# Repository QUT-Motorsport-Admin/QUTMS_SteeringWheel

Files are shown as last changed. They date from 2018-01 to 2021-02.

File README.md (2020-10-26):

QUTMS_Banner

# QUT Motorsport - Steering Wheel

### What?
A 'dumb' output terminal that acts as a digital dashboard for the car.
### Why?
To display information from the Chassis Controller (originating from various car sensors and systems) to the driver.
### How?
The steering wheel receives information over CANBUS from the Chassis Controller and displays the information relevant to the currently selected mode on a digital display. There will be two cylindrical switches that can be rotated to set the program to different modes allowing for the driver to view different sets of information on the display at will.
### Where?
A digital display in the steering wheel of the car that receives and displays information from other car systems to the driver.
### Who?
*Insert anyone who has worked on the software here.*

## Specific README's
These will cover any specific features, outlines or documentation that a programmer/designer should know about. Any specifics, or this outside the overview/outline please update an entry in the wiki

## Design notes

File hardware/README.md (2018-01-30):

# Steering Wheel Hardware

No hardware yet

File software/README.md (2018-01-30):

# Steering Wheel Software

The steering wheel could be considered a dumb terminal that shows the status of the car. It will be the only way to view the systems in the car aside from the C# program.

It will allow you to shift though the multiple modes that the Chassis Controller ([QUTMS_ChassisController](https://github.com/Technosasquach/QUTMS_ChassisController "QUTMS_ChassisController")) is capable off. It would then update the display and dash to what is best suited for the mode. Additonaly it could be programmed with different interfaces that show various elements of the car to the driver while racing. 

If you are working on this code, then its recommended that you talk to someone that would be driving, so you can tailor the software to their needs.

Below is a rough outline of its operations procedures.

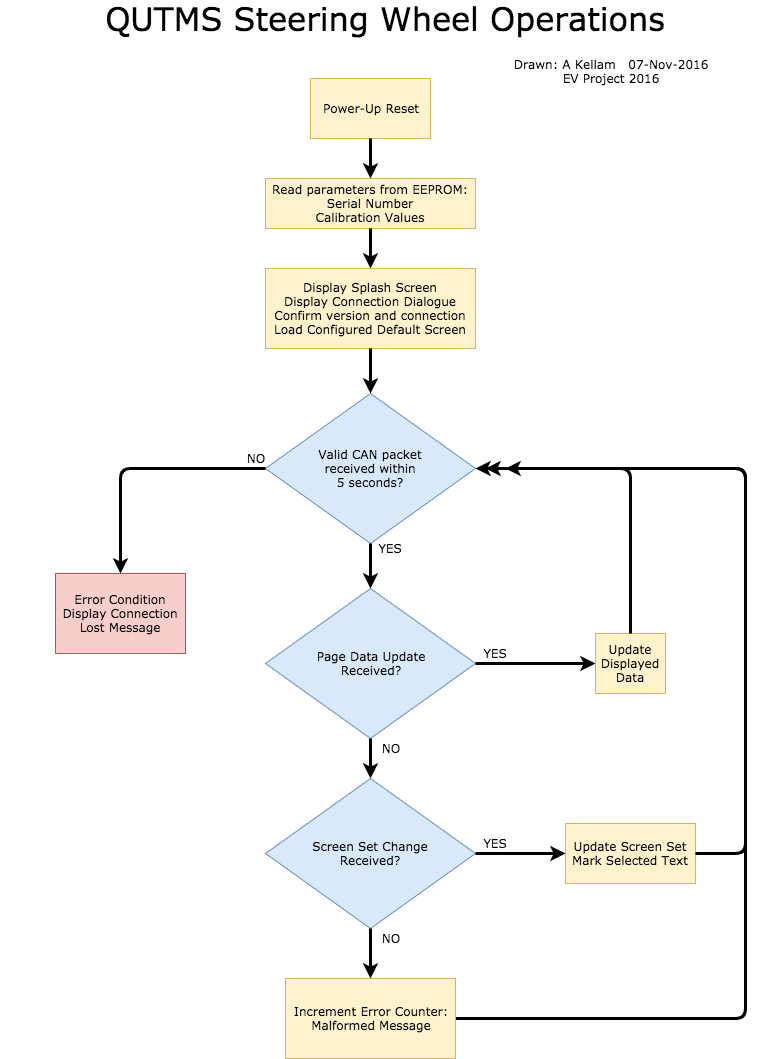
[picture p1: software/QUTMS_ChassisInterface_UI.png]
Steering Wheel


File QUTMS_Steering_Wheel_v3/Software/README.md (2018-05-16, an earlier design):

# Steering Wheel Software

The steering wheel could be considered a dumb terminal that shows the status of the car. It will be the only way to view the systems in the car aside from the C# program.

It will allow you to shift though the multiple modes that the Chassis Controller ([QUTMS_ChassisController](https://github.com/Technosasquach/QUTMS_ChassisController "QUTMS_ChassisController")) is capable off. It would then update the display and dash to what is best suited for the mode. Additonaly it could be programmed with different interfaces that show various elements of the car to the driver while racing.

If you are working on this code, then its recommended that you talk to someone that would be driving, so you can tailor the software to their needs.

Below is a rough outline of its operations procedures.

Steering Wheel

## Dashboard Design Analysis

Based on a team survey, these are the features of highest priority that need to be implemented into the steering wheel software.

| Highest Priority Features | N&deg;| Additional Info |
| :--- |:-----:| :--- |
| Speed | 14 | |
| Battery amount | 11 | kWh/km? |
| Heat | 9 | Endurance, accel, skidpad, 2WD, 4WD |
| Emergency info overrride  | 6 | |
| Race mode | 5 | |
| Lap timer / # | 5 | |
| Torque output | 3 | |
| Energy efficiency | 3 | |
| Accumulator energy | 2 | |
| Accel, brake levels | 2 | |

These are additional, lower priority features.

| Extra Features | N&deg; | Additional Info |
| :--- |:---:| :--- |
| Party Parrot loading screen | 6 | |
| Start / stop kill switch | 1 | |
| Lateral G's | 1 | Car lean |
| VTEC engaged | 1 | Tacho |
| Tyre pressure | 1 | |
| Regen efficiency | 1 | |
| Radio button | 1 | |
| Brake bias adjust (auto) | 1 | |
| Throttle application | 1 | |
| Traction/power per wheel | 1 | |
| Button input (+interactivity) and parameter control | 1 |

**Comments:**

- Big letters and numbers
- Colours used (appropriately)
- UI intuitive
- Wheel rotates around the dashboard, so no upside-down screens
- Clean and concise display - nothing unnecessary
- Diagnostic screen display relevant to an extreme condition (excessive G's &rarr; G-force reading warning)
- Set of comprehensive dashboard/diagnostic screens
- Ergonomic, light-weight, robust
- Input config/check config without config software
- Light predictive elements (fuel, temp)

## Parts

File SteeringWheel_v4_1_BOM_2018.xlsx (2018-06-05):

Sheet: SteeringWheel_v4_1
Part Type | Value | MFG Part Number | MFG | Reseller | Reseller Part Number | Board | Hyperlink | Description | Required Quantity | Unit Price | Quantity Ordered | Total | Footprint | Designator
Capacitor | 1uF | CL10B105KA8NNNC | Samsung Electro-Mechanics America, Inc. | Digikey | 1276-1184-1-ND | Steering Wheel | http://www.digikey.com.au/product-detail/en/samsung-electro-mechanics-america-inc/CL10B105KA8NNNC/1276-1184-1-ND/3889270 | Capacitor - 1uF Ceramic | 1 | 0.14 |  | 0 | 1608[0603] | C1
Capacitor | 10uF | GRM188R61E106MA73D | Murata Electronics North America | Digikey | 490-7202-1-ND | Steering Wheel | http://www.digikey.com.au/product-detail/en/murata-electronics-north-america/GRM188R61E106MA73D/490-7202-1-ND/3900486 | Capacitor - 10uF Ceramic | 3 | 0.49 |  | 0 | 1608[0603] | C3,C7,C13
Capacitor | 18pF | CL10C180JB8NNNC | Samsung Electro-Mechanics America, Inc. | Digikey | 1276-1089-1-ND | Steering Wheel | http://www.digikey.com.au/product-detail/en/samsung-electro-mechanics-america-inc/CL10C180JB8NNNC/1276-1089-1-ND/3889175 | Capacitor - 18pF Ceramic | 2 | 0.14 |  | 0 | 1608[0603] | C4,C5
Capacitor | 100nF | 06033C104KAT2A | AVX Corporation | Digikey | 478-3714-1-ND | Steering Wheel | http://www.digikey.com.au/product-detail/en/avx-corporation/06033C104KAT2A/478-3714-1-ND/1116412 | Capacitor - 100nF Ceramic | 4 | 0.14 |  | 0 | 1608[0603] | C6,C8,C9,C10
Capacitor | 0.33uF | C1608X5R1E334K080AC | TDK Corporation | Digikey | 445-5142-1-ND | Steering Wheel | http://www.digikey.com.au/product-detail/en/tdk-corporation/C1608X5R1E334K080AC/445-5142-1-ND/2093757 | Capacitor - 0.33uF Ceramic | 1 | 0.15 |  | 0 | 1608[0603] | C12
Inductor | 10uH | LBR2012T100K | Taiyo Yuden | Digikey | 587-2045-1-ND | Steering Wheel | http://www.digikey.com.au/product-detail/en/taiyo-yuden/LBR2012T100K/587-2045-1-ND/1788992 | Inductor | 1 | 0.14 |  | 0 | 2012[0805]_IND | L1
Column |  | 68016-106HLF | Amphenol FCI | Digikey | 609-3313-ND | Steering Wheel | http://www.digikey.com.au/product-detail/en/amphenol-fci/68016-106HLF/609-3313-ND/1878482 | Header, 6-Pin, Right Angle | 1 | 0.61 |  | 0 | HDR1X6H | P1
AtmelISPHeader | Are we using pogo pins? |  |  | Digikey |  | Steering Wheel |  | AtmelISPHeader | 1 |  |  | 0 | AtmelISPHeader
OLED |  | ER-OLEDM028-1Y | BuyDisplay | BuyDisplay | ER-OLEDM028-1Y | Steering Wheel | http://www.buydisplay.com/default/spi-2-8-inch-oled-arduino-256x64-graphic-module-with-pcb-yellow-on-black | OLED Display (PRICE: USD) | 1 | 23.55 | 5 | 117.75
OLED Header - Male to Male |  | PRPC008DAAN-RC | Sullins Connector Solutions | Digikey | S2011EC-08-ND | Steering Wheel | http://www.digikey.com.au/product-detail/en/sullins-connector-solutions/PRPC008DAAN-RC/S2011EC-08-ND/2775286 | Male-to-male Header, 8-Pin, Dual row | 1 | 0.72 |  | 0
OLED Header- Male to Female |  | PPTC082LFBN-RC | Sullins Connector Solutions | Digikey | S7076-ND | Steering Wheel | http://www.digikey.com.au/product-detail/en/sullins-connector-solutions/PPTC082LFBN-RC/S7076-ND/810214 | Male-to-female Header, 8-Pin, Dual row | 1 | 1.68 |  | 0 | HDR2X8 | P3
BTN Header - Male to Male - RA |  | 961102-5604-AR | 3M | Digikey | 3M9467-ND | Steering Wheel | http://www.digikey.com.au/product-detail/en/3m/961102-5604-AR/3M9467-ND/2071508 | Male-to-male Header, 2-Pin | 2 | 0.27 |  | 0 | HDR1X2 | P4,P5
PADL Header - Male to Male - RA |  | 961102-5604-AR | 3M | Digikey | 3M9467-ND | Steering Wheel | http://www.digikey.com.au/product-detail/en/3m/961102-5604-AR/3M9467-ND/2071508 | Male-to-male Header, 2-Pin | 2 | 0.27 |  | 0 | HDR1X2 | P7,P8
Wheel Push Button |  |  | Jaycar | Jaycar | SP0732 | Steering Wheel | https://www.jaycar.com.au/switch-push-watprf-mom-spst-5adc-d-30mm/p/SP0732 | Waterproof Switch | 2 | 4.95 |  | 0
Paddle Button | N/A on current version |  |  |  |  | Steering Wheel
Resistor | 1k | RC0805FR-071KL | Yageo | Digikey | 311-1.00KCRCT-ND | Steering Wheel | http://www.digikey.com.au/product-detail/en/yageo/RC0805FR-071KL/311-1.00KCRCT-ND/730391 | Resistor | 2 | 0.14 |  | 0 | 2012[0805]_Res | R1,R2
Resistor | 4k7 | RC0805FR-074K7L | Yageo | Digikey | 311-4.70KCRCT-ND | Steering Wheel | http://www.digikey.com.au/product-detail/en/yageo/RC0805FR-074K7L/311-4.70KCRCT-ND/730876 | Resistor | 26 | 0.14 |  | 0 | 2012[0805]_Res | R3-R26, R31-R34
Resistor | 10k | RC0805FR-0710KL | Yageo | Digikey | 311-10.0KCRCT-ND | Steering Wheel | http://www.digikey.com.au/product-detail/en/yageo/RC0805FR-0710KL/311-10.0KCRCT-ND/730482 | Resistor | 1 | 0.14 |  | 0 | 2012[0805]_Res | R35
SW_13 |  |  | Jaycar | Jaycar | SR1210 | Steering Wheel | https://www.jaycar.com.au/1-pole-sealed-pcb-rotary/p/SR1210 | 12 Position Switch | 2 | 3.95 |  | 0 | 13SW | SW1, SW2
ATmega64M1-AU | TRAY PART | ATMEGA64M1-AU | Atmel | Digikey | ATMEGA64M1-AU-ND | Steering Wheel | http://www.digikey.com.au/product-detail/en/atmel/ATMEGA64M1-AU/ATMEGA64M1-AU-ND/2271014 | 8-bit AVR Microcontroller | 1 | 11.28 |  | 0 | 32A_N | U1
TJA1040 |  | TJA1040T/CM,118 | NXP USA Inc. | Digikey | 568-10289-1-ND | Steering Wheel | http://www.digikey.com.au/product-detail/en/nxp-usa-inc/TJA1040T-CM,118/568-10289-1-ND/4162434 | High speed CAN transceiver | 1 | 1.7 |  | 0 | SO8_L | U4
MC33269 |  | MC33269ST-3.3T3G | ON Semiconductor | Digikey | MC33269ST-3.3T3GOSCT-ND | Steering Wheel | http://www.digikey.com.au/product-detail/en/on-semiconductor/MC33269ST-3.3T3G/MC33269ST-3.3T3GOSCT-ND/2120818 | Voltage Regulator | 1 | 1.24 |  | 0 | SOT223_N | VR1
Volt Reg (7805) |  | MIC5200-5.0YS | Microchip Technology | Digikey | 576-3380-5-ND | Steering Wheel | http://www.digikey.com.au/product-detail/en/microchip-technology/MIC5200-5.0YS/576-3380-5-ND/1030204 | Voltage Regulator | 1 | 1.4 |  | 0 | SOT223_N | VR2
XTAL - 16MHz |  | ABLS-16.000MHZ-D-4-T | Abracon LLC | Digikey | 535-13436-1-ND | Steering Wheel | http://www.digikey.com.au/product-detail/en/abracon-llc/ABLS-16.000MHZ-D-4-T/535-13436-1-ND/5980112 | Crystal Oscillator | 1 | 0.33 |  | 0 | Crystal | Y1
Nylon Standoff | M3 (11mm long) | R30-6701194 | Harwin Inc. | Digikey | 952-1532-ND | Steering Wheel | http://www.digikey.com.au/product-detail/en/harwin-inc/R30-6701194/952-1532-ND/2264513 | Standoff | 4 | 0.78 |  | 0
Nylon Screw | M3 (6.35mm shaft) | NMS-306 | Essentra Components | Digikey | RP808-ND | Steering Wheel | http://www.digikey.com.au/product-detail/en/essentra-components/NMS-306/RP808-ND/392957 | Screw for Standoffs | 8 | 0.44 |  | 0
 |  |  |  |  |  |  |  |  |  |  |  |  |  |  | Total: | 117.75

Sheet: SteeringWheel_v4_1_2018Order
Part Type | Value | MFG Part Number | MFG | Reseller | Reseller Part Number | Board | Hyperlink | Description | Required Quantity | Unit Price | Quantity Ordered | Proberble Cost | Total | Footprint | Designator
Capacitor | 1uF | GCJ188R71E105KA01D | Samsung Electro-Mechanics (https://www.digikey.com.au/en/supplier-centers/s/samsung-electro-mechanics-america) | Digikey | 490-14409-1-ND | Steering Wheel | https://www.digikey.com.au/product-detail/en/murata-electronics-north-america/GCJ188R71E105KA01D/490-14409-1-ND/6606870 | Capacitor - 1uF Ceramic | 1 | 0.4 |  | 0.4 | 0 | 1608[0603] | C1
Capacitor | 10uF | C1608X5R1A106K080AC | TDK Corporation (https://www.digikey.com.au/en/supplier-centers/t/tdk) | Digikey | 445-7486-1-ND | Steering Wheel | https://www.digikey.com.au/product-detail/en/tdk-corporation/C1608X5R1A106K080AC/445-7486-1-ND/2733558 | Capacitor - 10uF Ceramic | 3 | 0.68 |  | 2.04 | 0 | 1608[0603] | C3,C7,C13
Capacitor | 18pF | CL10C180JB8NFNC | Samsung Electro-Mechanics (https://www.digikey.com.au/en/supplier-centers/s/samsung-electro-mechanics-america) | Digikey | 1276-2209-1-ND | Steering Wheel | https://www.digikey.com.au/product-detail/en/samsung-electro-mechanics/CL10C180JB8NFNC/1276-2209-1-ND/3890295 | Capacitor - 18pF Ceramic | 2 | 0.15 |  | 0.3 | 0 | 1608[0603] | C4,C5
Capacitor | 100nF | C1608X7R1E104K080AA | TDK Corporation (https://www.digikey.com.au/en/supplier-centers/t/tdk) | Digikey | 445-1316-1-ND | Steering Wheel | https://www.digikey.com.au/product-detail/en/tdk-corporation/C1608X7R1E104K080AA/445-1316-1-ND/567697 | Capacitor - 100nF Ceramic | 4 | 0.14 |  | 0.56 | 0 | 1608[0603] | C6,C8,C9,C10
Capacitor | 0.33uF | C1608X5R1E334K080AC | TDK Corporation (https://www.digikey.com.au/en/supplier-centers/t/tdk) | Digikey | 445-5142-1-ND | Steering Wheel | https://www.digikey.com.au/product-detail/en/tdk-corporation/C1608X5R1E334K080AC/445-5142-1-ND/2093757 | Capacitor - 0.33uF Ceramic | 1 | 0.15 |  | 0.15 | 0 | 1608[0603] | C12
Inductor | 10uH | LBR2012T100K | Taiyo Yuden | Digikey | 587-2045-1-ND | Steering Wheel | http://www.digikey.com.au/product-detail/en/taiyo-yuden/LBR2012T100K/587-2045-1-ND/1788992 | Inductor | 1 | 0.15 |  | 0.15 | 0 | 2012[0805]_IND | L1
Column |  | 68016-106HLF | Amphenol FCI | Digikey | 609-3313-ND | Steering Wheel | http://www.digikey.com.au/product-detail/en/amphenol-fci/68016-106HLF/609-3313-ND/1878482 | Header, 6-Pin, Right Angle | 1 | 0.65 |  | 0.65 | 0 | HDR1X6H | P1
AtmelISPHeader | Are we using pogo pins? |  |  | Digikey |  | Steering Wheel |  | AtmelISPHeader | 1 |  |  | 0 | 0 | AtmelISPHeader
OLED |  | ER-OLEDM028-1Y | BuyDisplay | BuyDisplay | ER-OLEDM028-1Y | Steering Wheel | http://www.buydisplay.com/default/spi-2-8-inch-oled-arduino-256x64-graphic-module-with-pcb-yellow-on-black | OLED Display (PRICE: USD) | 1 | 23.55 | 5 | 23.55 | 117.75
OLED Header - Male to Male |  | PRPC008DAAN-RC | Sullins Connector Solutions | Digikey | S2011EC-08-ND | Steering Wheel | http://www.digikey.com.au/product-detail/en/sullins-connector-solutions/PRPC008DAAN-RC/S2011EC-08-ND/2775286 | Male-to-male Header, 8-Pin, Dual row | 1 | 0.73 |  | 0.73 | 0
OLED Header- Male to Female |  | PPTC082LFBN-RC | Sullins Connector Solutions | Digikey | S7076-ND | Steering Wheel | http://www.digikey.com.au/product-detail/en/sullins-connector-solutions/PPTC082LFBN-RC/S7076-ND/810214 | Male-to-female Header, 8-Pin, Dual row | 1 | 1.37 |  | 1.37 | 0 | HDR2X8 | P3
BTN Header - Male to Male - RA |  | 929835-01-02-RK | 3M | Digikey | 3M156872-02-ND | Steering Wheel | https://www.digikey.com.au/product-detail/en/3m/929835-01-02-RK/3M156872-02-ND/1093859 | Male-to-male Header, 2-Pin | 2 | 0.59 |  | 1.18 | 0 | HDR1X2 | P4,P5
PADL Header - Male to Male - RA |  | 929835-01-02-RK | 3M | Digikey | 3M156872-02-ND | Steering Wheel | https://www.digikey.com.au/product-detail/en/3m/929835-01-02-RK/3M156872-02-ND/1093859 | Male-to-male Header, 2-Pin | 2 | 0.59 |  | 1.18 | 0 | HDR1X2 | P7,P8
Wheel Push Button |  |  | Jaycar | Jaycar | SP0732 | Steering Wheel | https://www.jaycar.com.au/switch-push-watprf-mom-spst-5adc-d-30mm/p/SP0732 | Waterproof Switch | 2 | 4.95 |  | 9.9 | 0
Paddle Button | N/A on current version |  |  |  |  | Steering Wheel |  |  |  |  |  | 0 | 0
Resistor | 1k | RC0805FR-071KL | Yageo | Digikey | 311-1.00KCRCT-ND | Steering Wheel | http://www.digikey.com.au/product-detail/en/yageo/RC0805FR-071KL/311-1.00KCRCT-ND/730391 | Resistor | 2 | 0.14 |  | 0.28 | 0 | 2012[0805]_Res | R1,R2
Resistor | 4k7 | RC0805FR-074K7L | Yageo | Digikey | 311-4.70KCRCT-ND | Steering Wheel | http://www.digikey.com.au/product-detail/en/yageo/RC0805FR-074K7L/311-4.70KCRCT-ND/730876 | Resistor | 26 | 0.14 |  | 3.64 | 0 | 2012[0805]_Res | R3-R26, R31-R34
Resistor | 10k | RC0805FR-0710KL | Yageo | Digikey | 311-10.0KCRCT-ND | Steering Wheel | http://www.digikey.com.au/product-detail/en/yageo/RC0805FR-0710KL/311-10.0KCRCT-ND/730482 | Resistor | 1 | 0.14 |  | 0.14 | 0 | 2012[0805]_Res | R35
SW_13 |  |  | Jaycar | Jaycar | SR1210 | Steering Wheel | https://www.jaycar.com.au/1-pole-sealed-pcb-rotary/p/SR1210 | 12 Position Switch | 2 | 3.95 |  | 7.9 | 0 | 13SW | SW1, SW2
ATmega64M1-AU | TRAY PART | ATMEGA64M1-AU | Atmel | Digikey | ATMEGA64M1-AU-ND | Steering Wheel | http://www.digikey.com.au/product-detail/en/atmel/ATMEGA64M1-AU/ATMEGA64M1-AU-ND/2271014 | 8-bit AVR Microcontroller | 1 | 7.43 |  | 7.43 | 0 | 32A_N | U1
TJA1040 |  | TJA1040T/CM,118 | NXP USA Inc. | Digikey | 568-10289-1-ND | Steering Wheel | http://www.digikey.com.au/product-detail/en/nxp-usa-inc/TJA1040T-CM,118/568-10289-1-ND/4162434 | High speed CAN transceiver | 1 | 1.89 |  | 1.89 | 0 | SO8_L | U4
SPX1117M3 |  | SPX1117M3-L-3-3/TR | Exar Corporation (https://www.digikey.com.au/en/supplier-centers/e/exar-corporation) | Digikey | 1016-1848-1-ND | Steering Wheel | https://www.digikey.com.au/product-detail/en/exar-corporation/SPX1117M3-L-3-3-TR/1016-1848-1-ND/3586565 | Voltage Regulator | 1 | 0.68 |  | 0.68 | 0 | SOT223_N | VR1
Volt Reg (7805) |  | MIC5200-5.0YS | Microchip Technology | Digikey | 576-3380-5-ND | Steering Wheel | http://www.digikey.com.au/product-detail/en/microchip-technology/MIC5200-5.0YS/576-3380-5-ND/1030204 | Voltage Regulator | 1 | 1.47 |  | 1.47 | 0 | SOT223_N | VR2
XTAL - 16MHz |  | ABLS-16.000MHZ-D-4-T | Abracon LLC | Digikey | 535-13436-1-ND | Steering Wheel | http://www.digikey.com.au/product-detail/en/abracon-llc/ABLS-16.000MHZ-D-4-T/535-13436-1-ND/5980112 | Crystal Oscillator | 1 | 0.69 |  | 0.69 | 0 | Crystal | Y1
Nylon Standoff | M3 (11mm long) | R30-6701194 | Harwin Inc. | Digikey | 952-1532-ND | Steering Wheel | http://www.digikey.com.au/product-detail/en/harwin-inc/R30-6701194/952-1532-ND/2264513 | Standoff | 4 | 0.79 |  | 3.16 | 0
Nylon Screw | M3 (6.35mm shaft) | NMS-306 | Essentra Components | Digikey | RP808-ND | Steering Wheel | http://www.digikey.com.au/product-detail/en/essentra-components/NMS-306/RP808-ND/392957 | Screw for Standoffs | 8 | 0.25 |  | 2 | 0
 |  |  |  |  |  |  |  |  |  |  |  |  |  |  |  | Total: | 117.75

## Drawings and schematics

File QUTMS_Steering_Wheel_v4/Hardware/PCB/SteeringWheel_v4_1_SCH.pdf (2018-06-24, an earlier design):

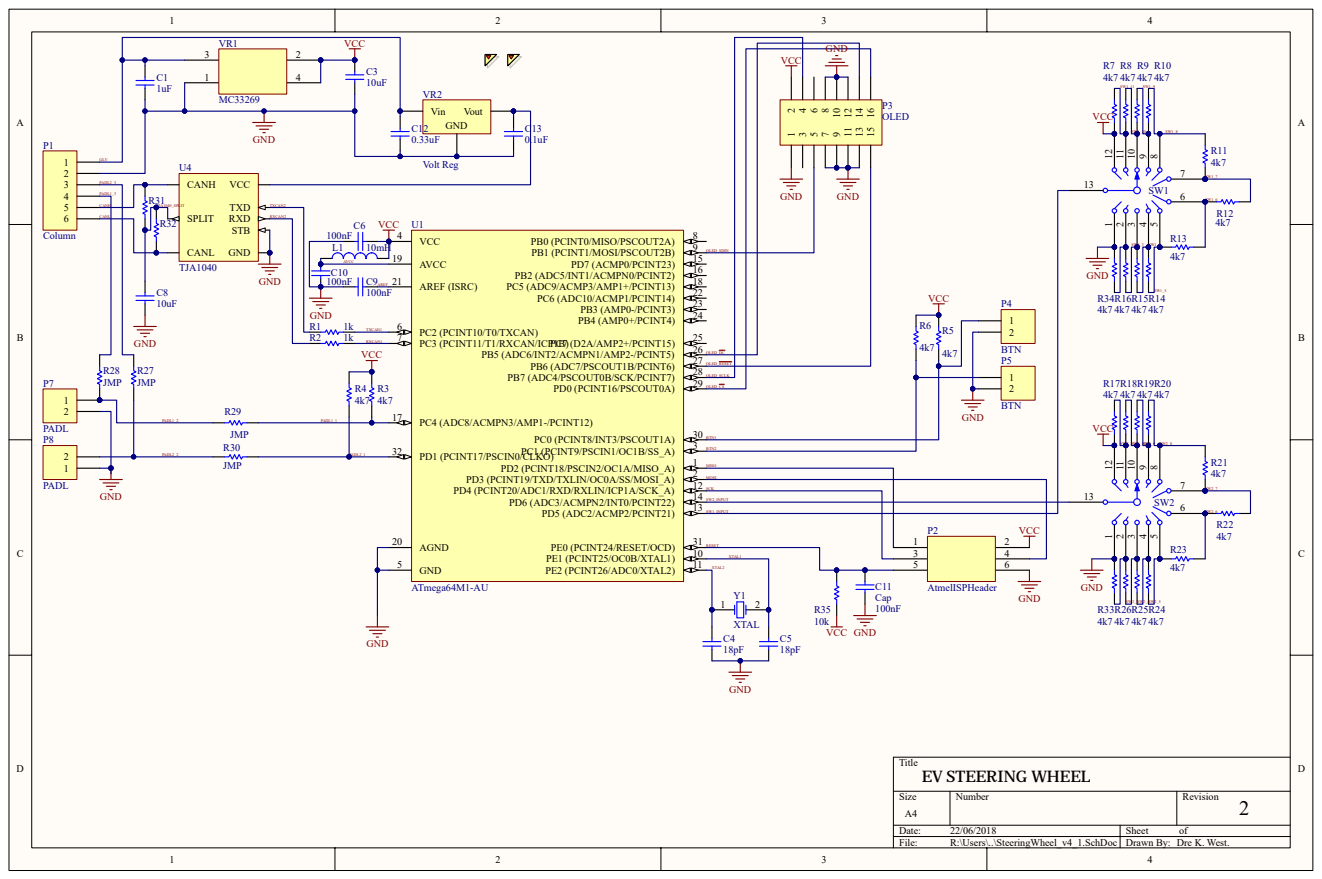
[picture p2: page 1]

Size A4 | Number | Revision 2

Date: 22/06/2018 | Sheet of
File: R:\Users\..\SteeringWheel_v4_1.SchDoc | Drawn By: Dre K. West.

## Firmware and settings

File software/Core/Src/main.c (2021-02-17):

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
/* Includes ------------------------------------------------------------------*/
#include "main.h"
#include "can.h"
#include "spi.h"
#include "usart.h"
#include "gpio.h"

/* USER CODE BEGIN Includes */
#include <stdio.h>
#include "stm32_adafruit_lcd.h"
#include "lcd.h"
#include "QUTMS.h"
#include "stdbool.h"
#include "gui.h"
#include <string.h>
#include "../lvgl/lvgl.h"
#include "screen.h"

/* USER CODE END Includes */


/* USER CODE BEGIN PV */
// Car configuration
Drive_Mode current_drive_mode = STATIC_MODE;
extern Event_Profile current_event;
uint8_t selected_menu_option, max_menu_option;
UI_Screen current_screen = SM_SCREEN;
float accumul_volts = 50.0f, accumul_temp = 40.0f, gearbox_temp = 1.0f,
		inverter_temp = 20.0f, motor_temp = 49.0f, accumul_charge = 0.5f,
		accumul_delta = 0.0f;
float drawn_accumul_volts = 0.0f, drawn_accumul_temp = 0.0f,
		drawn_gearbox_temp = 0.0f, drawn_inverter_temp = 0.0f,
		drawn_motor_temp = 0.0f, drawn_accumul_charge = 0.0f,
		drawn_accumul_delta = 0.0f;
uint8_t total_laps = 0, current_lap = 1;
extern Driver_Profile drivers[4], current_driver;
extern Event_Profile events[4];

// Inputs
volatile bool activate_btn_pressed, back_btn_pressed;
volatile uint8_t active_btn_state = 0, back_btn_state = 0;
extern bool menu_pot_incremented, menu_pot_decremented, menu_pot_pressed;
uint8_t prev_pot_value, current_pot_value;
uint16_t raw;

/* USER CODE END PV */

void SystemClock_Config(void);
static void MX_NVIC_Init(void);
/* USER CODE BEGIN PFP */
void my_flush_cb(lv_disp_drv_t *disp_drv, const lv_area_t *area,
		lv_color_t *color_p);

/* USER CODE END PFP */

/**
 * @brief  The application entry point.
 * @retval int
 */
int main(void) {
	/* MCU Configuration--------------------------------------------------------*/

	/* Reset of all peripherals, Initializes the Flash interface and the Systick. */
	HAL_Init();

	/* USER CODE BEGIN Init */

	/* Initialise graphics library----------------------------------------------*/

	/* USER CODE END Init */

	/* Configure the system clock */
	SystemClock_Config();

	/* Initialize all configured peripherals */
	MX_GPIO_Init();
	MX_CAN_Init();
	MX_SPI1_Init();
	MX_SPI2_Init();
	MX_USART1_UART_Init();

	/* Initialize interrupts */
	MX_NVIC_Init();
	/* USER CODE BEGIN 2 */
	/** Create CAN Filter & Apply it to &CANBUS4, &CANBUS2 */
	BSP_LCD_Init();
	lv_init();
	/* USER CODE END 2 */

	/* Infinite loop */
	/* USER CODE BEGIN WHILE */

//	drawStartupScreen();
//	HAL_Delay(2000);
	/*******************************
	 *    DISPLAY DRIVERS DEMO     *
	 ******************************/

	/*A static or global variable to store the buffers*/
	static lv_disp_buf_t disp_buf;

	/*Static or global buffer(s). The second buffer is optional*/
	static lv_color_t buf_1[320 * 10];
	//static lv_color_t buf_2[320];

	/*Initialize `disp_buf` with the buffer(s) */
	lv_disp_buf_init(&disp_buf, buf_1, NULL, 320 * 10);

	lv_disp_drv_t disp_drv; /*A variable to hold the drivers. Can be local variable*/
	lv_disp_drv_init(&disp_drv); /*Basic initialization*/
	disp_drv.buffer = &disp_buf; /*Set an initialized buffer*/
	disp_drv.flush_cb = my_flush_cb; /*Set a flush callback to draw to the display*/
	lv_disp_t *disp;
	disp = lv_disp_drv_register(&disp_drv); /*Register the driver and save the created display objects*/

	screen_create();

	uint32_t curtime = HAL_GetTick();
	uint8_t current = 0;
	RTD_open();

	while (1) {
		/* USER CODE END WHILE */

		/* USER CODE BEGIN 3 */

		if (HAL_GetTick() - curtime > 10000) {
			if (current == 1) {
				current = 0;
				RTD_open();
			} else {
				current = 1;
				screen_create();
				event_select_open();
			}


		}

		//driver_select_open();
		//HAL_Delay(50);
		//event_select_open();
		lv_task_handler();
		HAL_Delay(5);
	}
	/* USER CODE END 3 */
}

void my_flush_cb(lv_disp_drv_t *disp_drv, const lv_area_t *area,
		lv_color_t *color_p) {
	/*The most simple case (but also the slowest) to put all pixels to the screen one-by-one*/
	int32_t x, y;

	int32_t x_size = area->x2 - area->x1;
	int32_t y_size = area->y2 - area->y1;

	//ILI9488_LCDMUTEX_PUSH();
	ili9488_SetDisplayWindow(area->x1, area->y1, x_size + 1, y_size + 1);
#if ILI9488_INTERFACE == 0
	LCD_IO_WriteCmd8(0x2C);

	for (y = area->y1; y <= area->y2; y++) {
		for (x = area->x1; x <= area->x2; x++) {
			lv_color_t og_col = *color_p;
			uint8_t b = og_col.ch.blue;
			uint8_t g = og_col.ch.green;
			uint8_t r = og_col.ch.red;

			uint16_t color = (((r * 4) & 0b11111) << 11)
					| (((g * 8) & 0b111111) << 5) | ((b * 8) & 0b11111);

			ili9488_write16to24(color);
			//BSP_LCD_DrawPixel(x, y, color);
			// ili9488_WritePixel(x, y, color);
			color_p++;
		}
	}

#elif ILI9488_INTERFACE == 1
    LCD_IO_WriteCmd8DataFill16(ILI9488_RAMWR, RGBCode, Xsize * Ysize);
    #endif
	//ILI9488_LCDMUTEX_POP();

	/* IMPORTANT!!!
	 * Inform the graphics library that you are ready with the flushing*/
	lv_disp_flush_ready(disp_drv);
}

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
/* USER CODE BEGIN 4 */
void HAL_GPIO_EXTI_Callback(uint16_t GPIO_Pin) {
	// When pulse A goes low, is pulse b low or high, if its high, then its a clockwise movement otherwise it is anti clockwise

//	if(GPIO_Pin == 1){
//		BSP_LCD_SetBackColor(LCD_COLOR_RED);
//		BSP_LCD_SetTextColor(LCD_COLOR_RED);
//		BSP_LCD_FillRect(0, 0, 100, 100);
//	}
//	else if(GPIO_Pin == 2){
//		BSP_LCD_SetBackColor(LCD_COLOR_GREEN);
//		BSP_LCD_SetTextColor(LCD_COLOR_GREEN);
//		BSP_LCD_FillRect(0, 0, 100, 100);
//	}
}

/* USER CODE END 4 */
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


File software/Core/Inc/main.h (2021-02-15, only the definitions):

#define BACK_SW_Pin GPIO_PIN_2
#define BACK_SW_GPIO_Port GPIOA
#define ACTIVATE_SW_Pin GPIO_PIN_3
#define ACTIVATE_SW_GPIO_Port GPIOA
#define LED_B_Pin GPIO_PIN_4
#define LED_B_GPIO_Port GPIOF
#define ROT1_ENC_DEC_Pin GPIO_PIN_0
#define ROT1_ENC_DEC_GPIO_Port GPIOB
#define ROT1_ENC_INC_Pin GPIO_PIN_1
#define ROT1_ENC_INC_GPIO_Port GPIOB
#define ROT1_ENC_INC_EXTI_IRQn EXTI1_IRQn
#define ROT1_ENC_SW_Pin GPIO_PIN_8
#define ROT1_ENC_SW_GPIO_Port GPIOA
#define SCREEN_CS_Pin GPIO_PIN_10
#define SCREEN_CS_GPIO_Port GPIOC
#define SCREEN_D_C_Pin GPIO_PIN_11
#define SCREEN_D_C_GPIO_Port GPIOC
#define LED_A_Pin GPIO_PIN_2
#define LED_A_GPIO_Port GPIOD

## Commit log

2018-01-30 Initial Content Commit
    [SteeringWheel_v4_1_BOM_15_November_2016.xlsx, USBasp.sch]
2018-03-07 Update README's What, Why, How, Where, and Who
    Preliminary write-up of explaining What, Why, How, and Where for the steering wheel based off the software specific README. Haven't added anybody to the Who section because I'm unaware of who has wor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
2018-05-16 Steering Wheel V3
    [BOM.xlsx]
2018-05-20 Added crucial bitmaps for new function party_mode…
2018-06-05 Updated BOM for 2018 parts and orders (7-6-2018)
    [SteeringWheel_v4_1_BOM_15_November_2016.xlsx, SteeringWheel_v4_1_BOM_2018.xlsx]
2018-07-31 Latest steering wheel code from weekend work @ Anthony's - displays qutms splash then one screen set with 4 parameters including throttle percent
    [SteeringWheel_v6.PcbDoc]
2019-02-21 CAN and screen working. Minor bug in the Screen.
    [main.c]
2019-02-22 Thank god we dont clear the Recycle Bin everyday.
    [BOM.xlsx, SteeringWheel_v6.PcbDoc, USBasp.sch]
2019-06-13 Steering Wheel PCB V7 finalised
    [Board.PcbDoc, CAN.SchDoc, Control.SchDoc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]
2019-06-14 Board finished, exported gerbers. Freeze Rev1
    [Board.PcbDoc, Board.step, CAN.SchDoc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]
2019-06-15 Added something
    [Board.PcbDoc, Board.step]
2019-08-02 Remove QEV2 hardware designs.
    [Board.PcbDoc, Board.step, CAN.SchDoc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]
2020-09-27 Add software for QEV3 Steering Wheel LCD
2020-09-27 Revert "Add software for QEV3 Steering Wheel LCD"
    This reverts commit 5226c51a07c78c7eaad89e5ff4a08848d7d480ed.
    [lcd_io_spi.h, main.c, main.h]
2020-12-03 Port QEV3 GUI code to actual steering wheel board
2020-12-06 Improve accumulator bar rendering and logic, and fix bugs
    [gui.c, main.c]
2020-12-07 Configure back and activate button
2020-12-08 Add configuration and logic for rotary encoder for menu scrolling
2021-01-31 Improve UI, add more interation logic, and fix bugs
    [gui.c, main.c]
2021-02-17 updated to render correctly to screen
    TODO: need to clean up
    [main.c, screen.c]

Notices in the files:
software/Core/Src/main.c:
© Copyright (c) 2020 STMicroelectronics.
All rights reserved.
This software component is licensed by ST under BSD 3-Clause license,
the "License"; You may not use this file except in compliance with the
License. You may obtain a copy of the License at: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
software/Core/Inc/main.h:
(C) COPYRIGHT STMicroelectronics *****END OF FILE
